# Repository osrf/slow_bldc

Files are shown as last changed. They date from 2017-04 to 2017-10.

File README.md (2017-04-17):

# slow_bldc

## parts selection

### microcontrollers
Goal: Fast Cortex-M with FPU (at least for now). HS USB would be nice for tons of datalogging, but not necessarily required.
  * Selection: STM32F303CCT
  * Other parts considered:
    * STM32F723ZET6: a bit spendy but is fast with HS USB, which is neat.
    * STM32F4
      * Access line: F401, F410, F411, F412, F413 only have one ADC
      * Fancier ones have multiple ADC's which would be nicer.
    * Atmel SAM E / V / S

### motor driver
Goal: something completely-integrated with power capacity comfortable for 1A to 2A.
  * Selection: [TI DRV8312](http://www.ti.com/product/DRV8312)

### encoder
Requirements: SPI interface, relatively high resolution
  * Selection: AMS 5048A
    * 14 bit, SPI, 3.3v single-supply, 11 kHz
  * Other parts considered:
    * AMS AS5047D and AS5047P are intended for high-speed BLDC and automatically compensate for encoder latency
      * super cool, but probably not necessary for super low-speed applications
    * Melexis MLX90316
      * 12 bit, SPI
      * 5V supply
      * 1 kHz
    * MPS MA700
      * 3v3 supply, only 7 mA
      * 11 bit
      * 500 kHz
      * can be mounted off-axis and calibrated for donut magnets
    * Allegro A1335
      * 12 bit, SPI
      * can be mounted off-axis
    * AK7451
      * 12 bit
  * Analog output IC's are pretty difference since they output analog sine/cosine, which allows lots of flexibility would would require high-precision simultaneous-sampling ADC to be awesome
    * NXP KMZ60
    * KMT37
    * NVE AAT00x is super low power and tiny since it just provides the sine/cosine half bridges; you need to supply amps and ADC's
    * AS5115 has differential analog sine/cosine outputs

### comms
  * MCU has USB full-speed (12 mbps)
  * Half-duplex RS-485 IC included for chaining these boards together: SN65HVD75

### power supply
  * assumes a regulated 12V supply to provide both the gate-drive and motor bus voltage
  * onboard Recom DC-DC used to generate local 3.3v supply

### current sense
  * TI INA240 used for inline current measurement on flying series current-sense resistors to each phase lead

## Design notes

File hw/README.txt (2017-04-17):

designed to the no-touch specs at Sierra Circuits:
* 4 layers
* 6mil trace/space = 0.1524mm
* 10mil via hole size = 0.254mm
* 22mil via diameter = 0.5588mm
* 46mm circle outline = 1.811" x 1.811"

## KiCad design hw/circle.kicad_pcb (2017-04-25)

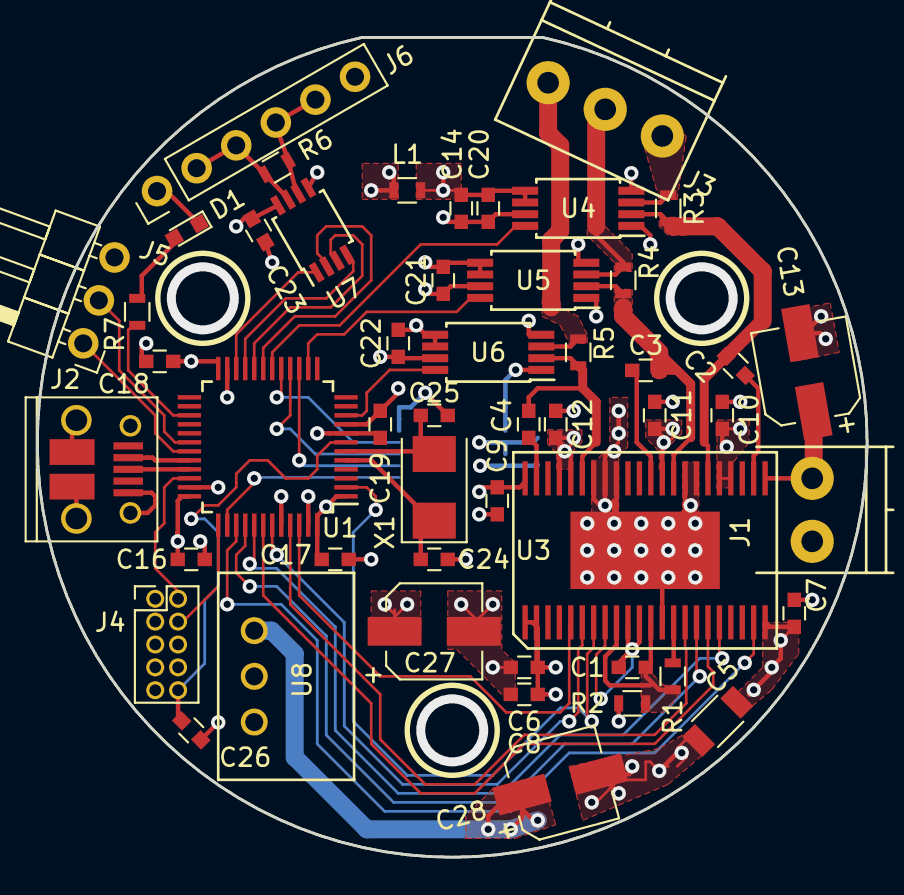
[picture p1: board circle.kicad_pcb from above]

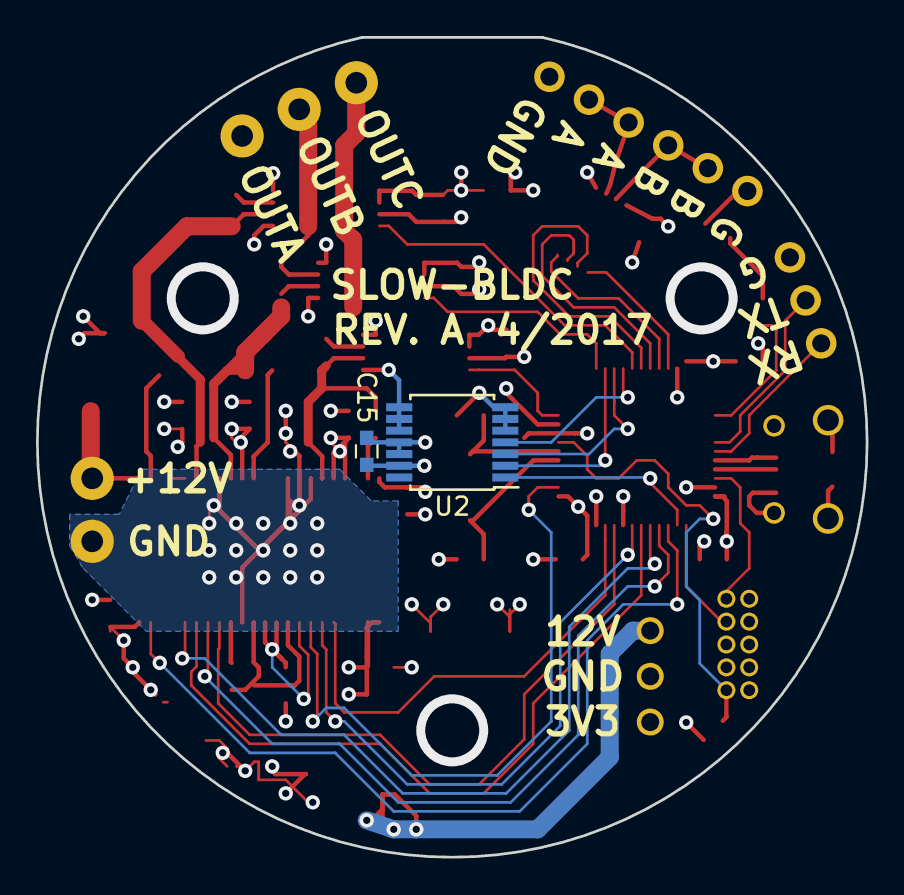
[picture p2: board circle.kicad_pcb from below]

Board: 4 copper layers, 46.1 x 45.5 mm, 52 parts (2 on the bottom side), 48 nets.

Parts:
C1, C2, C3, C4, C6, C10, C11, C12, C15, C16, C17, C18, C19, C20, C21, C22, C23, C26: 100n; C_0603
C5: 22u; C_1206
C7, C8, C9, C14: 1u; C_0603
C13, C27, C28: 100u; CP_Elec_5x5.8
C24, C25: 12p; C_0603
D1: LED_Small; LED_0603
J1: CONN_01X02; TerminalBlock_Pheonix_PT-3.5mm_2pol
J2: USB_OTG; USB_Micro-B_10103594-0001LF
J3: CONN_01X03; TerminalBlock_Pheonix_PT-3.5mm_3pol
J4: CONN_02X05; Pin_Header_Straight_2x05_Pitch1.27mm
J5: CONN_01X03; Pin_Header_Angled_1x03_Pitch2.54mm
J6: CONN_01X06; Pin_Header_Straight_1x06_Pitch2.54mm
L1: ferrite; R_0603
R1: 27k0; R_0603
R2: 1; R_0603
R3, R4, R5, R7: 0R05; R_0603
R6: 100; R_0603
U1: STM32F303CCTx; LQFP-48_7x7mm_Pitch0.5mm
U2: AS5048A; TSSOP-14_4.4x5mm_Pitch0.65mm
U3: DRV8312; SOIC-44-POWERPAD
U4, U5, U6: INA240; TSSOP-8_4.4x3mm_Pitch0.65mm
U7: SN65HVD75; TSSOP-8_3x3mm_Pitch0.65mm
U8: R-78xx-0.5
X1: 8 MHz; Crystal_SMD_5032-2pin_5.0x3.2mm

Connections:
+3V3: C15.2, C16.2, C17.2, C18.2, C23.2, C27.1, J4.1, L1.2, U1.1, U1.24, U1.36, U1.48, U2.11, U2.12, U7.8, U8.3
+12V: C5.2, C6.2, C7.2, C8.2, C9.2, C10.2, C11.2, C12.2, C13.1, C28.1, J1.2, U3.1, U3.2, U3.22, U3.23, U3.26, U3.27, U3.32, U3.40, U3.41, U3.44, U8.1
/AGND: C1.1, R1.1, R2.2, U3.9, U3.12
/AMPA: U1.18, U4.8
/AMPB: U1.14, U5.8
/AMPC: U1.10, U6.8
/BSTA: C2.2, U3.24
/BSTB: C3.2, U3.33
/BSTC: C4.2, U3.43
/ENC_CS: U1.38, U2.1
/ENC_MISO: U1.16, U2.3
/ENC_MOSI: U1.17, U2.4
/ENC_SCLK: U1.15, U2.2
/FAULT: U1.41, U3.18
/LED: R7.1, U1.27
/NRST: C26.2, J4.10, U1.7
/OCADJ: R1.2, U3.14
/OSC_IN: C24.2, U1.5, X1.1
/OSC_OUT: C25.2, U1.6, X1.2
/OTW: U1.39, U3.21
/OUTA: J3.1, R3.1, U4.3
/OUTB: J3.2, R4.1, U5.3
/OUTC: J3.3, R5.1, U6.3
/PWMA: U1.42, U3.17
/PWMB: U1.45, U3.15
/PWMC: U1.46, U3.5
/RS485A: J6.4, J6.5, R6.2, U7.6
/RS485B: J6.2, J6.3, R6.1, U7.7
/RS485DE: U1.20, U7.3
/RS485DI: U1.21, U7.4
/RS485RE: U1.19, U7.2
/RS485RO: U1.22, U7.1
/RSTA: U1.40, U3.16
/RSTB: U1.2, U3.7
/RSTC: U1.43, U3.6
/SENSEA: C2.1, R3.2, U3.28, U4.2
/SENSEB: C3.1, R4.2, U3.31, U5.2
/SENSEC: C4.1, R5.2, U3.39, U6.2
/STDIN: J5.1, U1.31
/STDOUT: J5.2, U1.30
/SWCLK: J4.4, U1.37
/SWDIO: J4.2, U1.34
/USBD+: J2.3, U1.33
/USBD-: J2.2, U1.32
/VREG: C1.2, U3.8, U3.10, U3.11
GND: C5.1, C6.1, C7.1, C8.1, C9.1, C10.1, C11.1, C12.1, C13.2, C14.1, C15.1, C16.1, C17.1, C18.1, C19.1, C20.1, C21.1, C22.1, C23.1, C24.1, C25.1, C26.1, C27.2, C28.2, D1.1, J1.1, J2.5, J2.6, J4.3, J4.5, J4.9, J5.3, J6.1, J6.6, R2.1, U1.8, U1.23, U1.35, U1.44, U1.47, U2.5, U2.6, U2.7, U2.8, U2.9, U2.10, U2.13, U3.13, U3.29, U3.30, U3.36, U3.37, U3.38, U3.45, U4.1, U4.4, U4.7, U5.1, U5.4, U5.7, U6.1, U6.4, U6.7, U7.5, U8.2
unnamed: D1.2, R7.2
VAA: C14.2, C19.2, C20.2, C21.2, C22.2, L1.1, U1.9, U4.5, U4.6, U5.5, U5.6, U6.5, U6.6

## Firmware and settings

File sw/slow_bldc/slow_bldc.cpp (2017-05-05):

#include <cstdio>
#include <cstdlib>
#include <stdint.h>
#include <vector>
#include "lightweightserial.h"
extern "C" {
#include "parser.h"
}
#include "ros/ros.h"
#include "slow_bldc/SetIntParam.h"
#include "slow_bldc/GetIntParam.h"

LightweightSerial *g_serial = NULL;

// this class models the state of the microcontroller
class MCU
{
public:
  std::map
};

static MCU g_mcu;

bool send_pkt(const uint8_t *pkt, const uint32_t len)
{
  if (len >= 252) {
    ROS_ERROR("refusing to send %d-byte packet. must be <252.",
        static_cast<int>(len));
    return false;
  }
  ROS_INFO("sending %d-byte packet", static_cast<int>(len));
  uint8_t framed_pkt[len+5];
  framed_pkt[0] = 0xbe;
  framed_pkt[1] = 0xef;
  framed_pkt[2] = static_cast<uint8_t>(len);
  uint16_t csum = static_cast<uint16_t>(len);
  for (uint32_t i = 0; i < len; i++) {
    framed_pkt[i+3] = pkt[i];
    csum += pkt[i];  // so bad. do something smarter someday.
  }
  framed_pkt[len+3] = static_cast<uint8_t>(csum & 0xff);
  framed_pkt[len+4] = static_cast<uint8_t>(csum >> 8);
  return g_serial->write_block(framed_pkt, len+5);
}

// this function spins forever or until max_seconds
bool rs485_spin(const double max_seconds, const uint8_t expected_pkt_id = 0)
{
  ros::Rate loop_rate(1000);
  ros::Time t_end = ros::Time::now() + ros::Duration(max_seconds);
  while (ros::ok()) {
    if (max_seconds > 0 && t_end < ros::Time::now())
      break;
    loop_rate.sleep();
    ros::spinOnce();
    uint8_t rx_byte = 0;
    while (g_serial->read(&rx_byte)) {
      //printf("rx: %02x\n", rx_byte);
      uint8_t rx_pkt_id = parser_process_byte(rx_byte);
      if (expected_pkt_id && expected_pkt_id == rx_pkt_id)
        return rx_pkt_id;
    }
  }
  return 0;
}

bool set_led(bool on)
{
  uint8_t pkt[2] = { 0x10, 0x00 };
  if (on)
    pkt[1] = 1;
  return send_pkt(pkt, sizeof(pkt));
}

bool get_num_params()
{
  uint8_t pkt[1] = { 0x01 };
  send_pkt(pkt, sizeof(pkt));
  ROS_INFO("calling rs485_spin...");
  rs485_spin(1.0, 0x01);
  ROS_INFO("back from rs485_spin...");
  return 42;
}

void rs485_rx_num_params(const uint32_t payload_len, const uint8_t *payload)
{
  ROS_INFO("rs485_rx_num_params()");
  if (payload_len != 4) {
    ROS_ERROR("unexpected payload len: %d", (int)payload_len);
    return;
  }
  const uint32_t num_params =
      payload[0] | (payload[1]<<8) | (payload[2]<<16) | (payload[3]<<24);
  ROS_INFO("num_params = %d", (int)num_params);
}

void rs485_rx_pkt(const uint32_t len, const uint8_t *data)
{
  ROS_INFO("rs485_rx_pkt(%d)", (int)len);
  if (len == 0) {
    ROS_ERROR("received zero-length rs485 packet");
    return;
  }
  const uint8_t pkt_id = data[0];
  switch(pkt_id)
  {
    case 0x01: rs485_rx_num_params(len-1, data+1); break;
    default: ROS_INFO("unrecognized packet ID: %02x", (int)pkt_id);
  }
}

bool set_int_param(slow_bldc::SetIntParam::Request &request,
    slow_bldc::SetIntParam::Response &response)
{
  int param_name_len = static_cast<int>(request.name.size());
  if (param_name_len > 250) {
    ROS_ERROR("param name len is too long: %s", request.name.c_str());
    return false;
  }
  ROS_INFO("set_int_param(%s, %d)",
      request.name.c_str(), request.value);
  uint8_t pkt[256] = {0};
  pkt[0] = 4;  // packet type 4 = set int param by name
  memcpy(&pkt[1], &request.value, 4);
  strcpy((char *)&pkt[5], request.name.c_str());
  return send_pkt(pkt, 6 + param_name_len);
}

bool get_int_param(slow_bldc::GetIntParam::Request &request,
    slow_bldc::GetIntParam::Response &response)
{
  int param_name_len = static_cast<int>(request.name.size());
  if (param_name_len > 250) {
    ROS_ERROR("param name len is too long: %s", request.name.c_str());
    return false;
  }
  ROS_INFO("get_int_param(%s, %d)",
      request.name.c_str(), request.value);
  uint8_t pkt[256] = {0};
  pkt[0] = 3;  // packet type 3 = get int param by name
  strcpy((char *)&pkt[1], request.name.c_str());
  if (!send_pkt(pkt, 2 + param_name_len))
    return false;
  if (!rs485_spin(0.5, 3)) {
    ROS_ERROR("didn't hear back from MCU for request for parameter [%s]",
        request.name.c_str());
    return false;
  }
  return 
}

int main(int argc, char **argv)
{
  ros::init(argc, argv, "slow_bldc");
  ros::NodeHandle nh, nh_private("~");
  std::string rs485_device;
  nh_private.param<std::string>("rs485_device", rs485_device, "/dev/ttyUSB0");
  g_serial = new LightweightSerial(rs485_device.c_str(), 1000000);
  if (!g_serial) {
    ROS_FATAL("couldn't open serial device");
    return 1;
  }
  ROS_INFO("opened %s", rs485_device.c_str());
  parser_init();
  parser_set_rx_pkt_fptr(rs485_rx_pkt);
  const int num_params = get_num_params();
  ROS_INFO("device has %d params", num_params);
  ros::ServiceServer int_param_srv =
      nh.advertiseService("set_int_param", set_int_param);
  rs485_spin(-1);  // spin forever. wooooahhh that makes me feel dizzy
  ROS_INFO("entering slow_bldc spin loop");
  return 0;
}

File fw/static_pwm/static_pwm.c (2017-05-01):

#include <stdio.h>
#include "current.h"
#include "led.h"
#include "motor.h"
#include "pwm.h"

int main(int argc, char **argv)
{
  printf("hello, world! I hope this works!\r\n");
  // test the pwm module
  const int16_t pwm[3] = { 1024-200, 1024+200, 1024 };
  motor_assert_reset(false);
  while (1) {
    for (volatile int i = 0; i < 200000; i++) { }
    led_toggle();
    pwm_set(pwm[0], pwm[1], pwm[2]);
  }
  return 0;
}

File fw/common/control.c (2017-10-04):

#include <stdio.h>
#include "control.h"
#include "enc.h"
#include "motor.h"
#include "param.h"
#include "pwm.h"
#include "systime.h"
#include "tables.h"

// define a float32 literal for pi:
#define PI 3.1415926f

#define CONTROL_MODE_IDLE     0
#define CONTROL_MODE_VOLTAGE  1
#define CONTROL_MODE_POSITION 2
static uint32_t g_control_mode = CONTROL_MODE_POSITION;
static uint32_t g_control_encoder_offset = 500;
#define ENC_TICKS_PER_ELEC_REV (ENC_COUNTS / MOTOR_POLE_PAIRS)
static volatile float g_voltage_target = 2.0;
static volatile float g_position_target = 0.6;
static volatile float g_position_kp = 80; //20.0;
static volatile float g_position_kd = 0.2;//0.1; //0.4;
static volatile float g_position_kd_alpha = 0.2;
static uint32_t g_control_prev_t = 0;

void control_init()
{
  printf("control_init()\n");
  param_add("control_mode", PARAM_TYPE_INT, &g_control_mode);
  param_add("encoder_offset", PARAM_TYPE_INT, &g_control_encoder_offset);
  param_add("voltage_target", PARAM_TYPE_FLOAT, &g_voltage_target);
  param_add("position_target", PARAM_TYPE_FLOAT, &g_position_target);
  param_add("position_kp", PARAM_TYPE_FLOAT, &g_position_kp);
  param_add("position_kd", PARAM_TYPE_FLOAT, &g_position_kd);
}

void control_tick()
{
  const uint32_t enc_ticks = enc_poll() + g_control_encoder_offset;
  const uint32_t elec_angle_ticks = enc_ticks % ENC_TICKS_PER_ELEC_REV;

  const uint32_t t_now = SYSTIME_USECS;
  uint32_t dt = t_now - g_control_prev_t;
  g_control_prev_t = t_now;
  if (dt > 10000)
    dt = 10000; // clamp dt to 10ms, in case it's gone totally bonkers

  float v_a = 0, v_b = 0, v_c = 0;  // relative to 1/2 bus voltage

  if (g_control_mode == CONTROL_MODE_POSITION) {
    const float enc_radians = enc_ticks * 2.0f * PI / ENC_COUNTS;
    float pos_error = g_position_target - enc_radians;
    if (pos_error > PI)
      pos_error -= 2.0f * PI;
    else if (pos_error < -PI)
      pos_error += 2.0f * PI;

    static float prev_error = 0;
    float d_error_est = (pos_error - prev_error) / (1.0e-6 * dt);
    static float d_error = 0;
    d_error =  g_position_kd_alpha * d_error_est +
              (1.0f - g_position_kd_alpha) * d_error;
    prev_error = pos_error;

    g_voltage_target = -g_position_kp * pos_error - g_position_kd * d_error;
  }

  if (g_control_mode == CONTROL_MODE_VOLTAGE ||
      g_control_mode == CONTROL_MODE_POSITION) {
    // calculate the indices of the A, B, C voltages (120 degrees apart)
    uint16_t th_a = elec_angle_ticks;
    if (th_a < 0)
      th_a += ENC_TICKS_PER_ELEC_REV;  // in case the offset is negative
    if (th_a >= ENC_TICKS_PER_ELEC_REV)
      th_a -= ENC_TICKS_PER_ELEC_REV;  // wrap back, in case offset wrapped us

    uint16_t th_b = th_a + TABLE_120_DEG;
    if (th_b >= ENC_TICKS_PER_ELEC_REV)
      th_b -= ENC_TICKS_PER_ELEC_REV;  // wrap

    uint16_t th_c = th_a + 2 * TABLE_120_DEG;
    if (th_c >= ENC_TICKS_PER_ELEC_REV)
      th_c -= ENC_TICKS_PER_ELEC_REV;  // wrap

    v_a = g_voltage_target * g_tables_motor_modulation[th_a];
    v_b = g_voltage_target * g_tables_motor_modulation[th_b];
    v_c = g_voltage_target * g_tables_motor_modulation[th_c];
  }

  const float PWM_MID = PWM_MAX / 2.0f;
  if (g_control_mode == CONTROL_MODE_IDLE) {
    pwm_set(PWM_MID, PWM_MID, PWM_MID);
  }
  else {
    const float BUS_VOLTAGE = 12.0f;
    int32_t pwm_a = (int32_t)(PWM_MID * v_a / BUS_VOLTAGE + PWM_MID);
    int32_t pwm_b = (int32_t)(PWM_MID * v_b / BUS_VOLTAGE + PWM_MID);
    int32_t pwm_c = (int32_t)(PWM_MID * v_c / BUS_VOLTAGE + PWM_MID);
    // clamp to sane values
    pwm_a = pwm_a < 0 ? 0 : pwm_a;
    pwm_b = pwm_b < 0 ? 0 : pwm_b;
    pwm_c = pwm_c < 0 ? 0 : pwm_c;
    pwm_a = pwm_a >= PWM_MAX ? PWM_MAX : pwm_a;
    pwm_b = pwm_b >= PWM_MAX ? PWM_MAX : pwm_b;
    pwm_c = pwm_c >= PWM_MAX ? PWM_MAX : pwm_c;
    pwm_set(pwm_a, pwm_b, pwm_c);
  }
}

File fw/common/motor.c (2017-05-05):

#include <stdio.h>
#include "motor.h"
#include "pin.h"
#include "st/stm32f303xc.h"

// motor-drive related pins:
#define OTW_GPIO GPIOB
#define OTW_PIN 3

#define FAULT_GPIO GPIOB
#define FAULT_PIN 5

#define RSTA_GPIO GPIOB
#define RSTA_PIN 4

#define RSTB_GPIO GPIOC
#define RSTB_PIN 13

#define RSTC_GPIO GPIOB
#define RSTC_PIN 7

void motor_init()
{
  printf("motor_init()\n");
  pin_set_input(OTW_GPIO, OTW_PIN, false);  // no internal pullup needed
  pin_set_input(FAULT_GPIO, FAULT_PIN, false);
  pin_set_output(RSTA_GPIO, RSTA_PIN, false);
  pin_set_output(RSTB_GPIO, RSTB_PIN, false);
  pin_set_output(RSTC_GPIO, RSTC_PIN, false);
  motor_assert_reset(true);
}

void motor_assert_reset(const bool reset)
{
  pin_set_output_state(RSTA_GPIO, RSTA_PIN, reset ? 0 : 1);
  pin_set_output_state(RSTB_GPIO, RSTB_PIN, reset ? 0 : 1);
  pin_set_output_state(RSTC_GPIO, RSTC_PIN, reset ? 0 : 1);
}

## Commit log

2017-04-03 stm32f4 notes
2017-04-10 encoder shopping
2017-04-10 more encoder searching
2017-04-10 more ams encoder options
2017-04-10 add encoder ic
    [circle.kicad_pcb, circle.sch]
2017-04-11 filling in the schematic
    [circle.kicad_pcb, circle.sch]
2017-04-11 rs485 transceiver
    [circle.kicad_pcb, circle.sch]
2017-04-12 power module selection
    [circle.sch]
2017-04-13 add r-78 dc/dc supply
    [circle.kicad_pcb, circle.sch]
2017-04-13 rs485 connector
    [circle.kicad_pcb, circle.sch]
2017-04-13 swd, etc.
    [circle.kicad_pcb, circle.sch]
2017-04-16 assign mcu pins
    [circle.kicad_pcb, circle.sch]
2017-04-16 mounting holes
    [circle.kicad_pcb]
2017-04-17 moving placements a bit to clear mounting holes
    [circle.kicad_pcb]
2017-04-17 initial placement complete
    [circle.kicad_pcb, circle.sch]
2017-04-17 power planes
    [circle.kicad_pcb]
2017-04-18 rev.A sent to fab
    [circle.kicad_pcb, circle.sch]
2017-04-18 add part numbers
    [circle.sch]
2017-04-25 clean up fab drawing for hand assembly
    [circle.kicad_pcb]
2017-04-26 fix led resistor value
    [circle.sch]
2017-05-01 fix build and get console working
    [console.c, main.cpp, rs485.c]
2017-05-01 bringing up board. encoder and motor driver IC seem fine.
    [circle.sch]
2017-05-02 software skeleton and beginning of params and rs485 in firmware
    [Driver.cfg]
2017-05-05 voltage control skeleton
2017-05-05 voltage mode control loop appears to be working.
